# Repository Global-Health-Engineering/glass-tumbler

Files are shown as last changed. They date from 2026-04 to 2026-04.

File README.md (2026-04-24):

<!-- badges: start -->



<!-- badges: end -->

<h1> Solar-Powered Glass Tumbler for Cape Maclear, Malawi: Design, Maintenance, Operation, and Results </h1>

**Contributors**

- **Emma Steinke** &mdash; [ORCID 0009-0005-9115-9379](https://orcid.org/0009-0005-9115-9379) &mdash; *design, construction, testing, writing*
- **Jakub Tkaczuk** &mdash; [ORCID 0000-0001-7997-9423](https://orcid.org/0000-0001-7997-9423) &mdash; *supervision, page development & maintenance*
- **Elizabeth Tilley** &mdash; [ORCID 0000-0002-2095-9724](https://orcid.org/0000-0002-2095-9724) &mdash; *supervision*

<br>
<p align="middle">

<br><br>
This work is certified by the Open Source Hardware Association.<br \>

<br>
<b>Complete description of system design, functionalities, operation, and maintenance is available on:<br \>
<a href="https://global-health-engineering.github.io/glass-tumbler/">Github pages</a>.
</b>
</p>

# Background

This repository details the construction, operation, and maintenance of the solar-powered glass tumbler built as part of a collaboration between the Malawian community-based organization, Sustainable Cape Maclear, and the Global Health Engineering Group at ETH Zürich.

Cape Maclear is a rural Malawian town located within a UNESCO World Heritage Site, which has attracted significant tourism and growth in the last 20 years. This has led to a unique waste challenge: an abundance of non-returnable glass bottles that are not part of a deposit system. The accumulation of broken glass creates sharp fragments that pose significant injury risks to residents, tourists, and wildlife.

Because industrial recycling is not economically or technically feasible in this location, the tumbler uses **glass tumbling** to grind away sharp edges, producing smooth "sea glass" that is safe for reuse in construction, landscaping, and jewelry. The machine is a standalone, solar-powered rotating drum system designed to process 20 kg batches of glass with a total material cost of approximately **$581.10**.



# PDF Documentation

The full detailed guide and the quick start guide are available in the [`doc`](doc/) directory:

- [`doc/detailed_guide.pdf`](doc/detailed_guide.pdf)  
- [`doc/quickstart_guide.pdf`](doc/quickstart_guide.pdf)

CAD models and technical drawings are available in the [`cad`](cad/) directory.

# License

Different parts of this repository are released under different licenses, following standard practice for open-hardware research projects:

| Component | License |
| :--- | :--- |
| Hardware design (CAD, drawings, STEP files in [`cad/`](cad/)) | [CERN-OHL-S v2](LICENSE.md) |
| Documentation (qmd pages, guides in [`doc/`](doc/), this README) | [CC-BY-4.0](doc/LICENSE.md) |
| Datasets ([`data/`](data/)) | [CC-BY-4.0](data/LICENSE.md) |

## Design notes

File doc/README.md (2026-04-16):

# Documentation

PDF guides for the solar-powered glass tumbler.

| File | Description |
| :--- | :--- |
| [`detailed_guide.pdf`](detailed_guide.pdf) | Comprehensive manual covering the full system description, troubleshooting, electrical schematics, and repair procedures. |
| [`quickstart_guide.pdf`](quickstart_guide.pdf) | Short operator-facing guide for daily loading, running, and unloading of the tumbler. |

The rendered HTML version of the user-facing content lives on the project's [GitHub Pages site](https://global-health-engineering.github.io/glass-tumbler/).

## Licensing

The PDF guides in this directory are released under [Creative Commons Attribution 4.0 International (CC-BY-4.0)](LICENSE.md). The hardware design at the repository root is under [CERN-OHL-S v2](../LICENSE.md).

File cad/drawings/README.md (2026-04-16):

# Technical Drawings

2D manufacturing drawings for individual parts and the full assembly. All dimensions in millimetres.

| File | Contents |
| :--- | :--- |
| `fullTumbler.pdf` | Full assembly drawing with part callouts. |
| `mainFrame.pdf` | Outer (main) frame — 80 mm x 40 mm x 2 mm steel beams. |
| `innerFrame.pdf` | Inner (drum) frame — 30 mm x 30 mm x 2 mm steel beams. |
| `drumAndShaft.pdf` | Drum with shaft assembly (LPG cylinder body, 25 mm shaft). |
| `flange.pdf` | Custom lathe-turned flange connecting the shaft to the drum. |
| `drumLid.pdf` | Hexagonal drum lid with toggle-latch geometry and seal lining. |

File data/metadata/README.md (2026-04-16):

# GENERAL INFORMATION

* Title of Dataset: Solar-Powered Glass Tumbling Efficiency Analysis
* Author Information:
    * Name: Emma Steinke
    * Institution: Global Health Engineering Lab, ETH Zürich
    * Email: steinkee@ethz.ch

* Date of data collection: October 2025 - February 2026
* Geographic location of data collection: Cape Maclear, Malawi 

# SHARING/ACCESS INFORMATION

* Licenses/restrictions placed on the data: CC-BY
* Was data derived from another source? Yes
    * If yes, list source(s): Solar Irradiance data sourced from Solcast API.

# DATA & FILE OVERVIEW

## File List:
* **glass_brightness.csv**: Raw data containing pixel brightness measurements for glass samples at various tumbling durations.
* **imperfections.csv**: Raw counts of physical imperfections across different glass batches and abrasive media.
* **irradiance_data_2024.csv**: Meteorological data including Global Horizontal Irradiance (GHI), cloud opacity, and air temperature for the year 2024.
* **derived_lifetime_costs.csv**: Calculated financial projections comparing the cost per 100 kg of treated material over the system's lifetime.
* **glass_brightness_averages.csv**: Processed dataset providing the mean brightness values for each glass treatment category over time.
* **imperfections_averages.csv**: Processed dataset providing the average number of imperfections for each glass treatment category.
* **tumbler_start_260W.csv**: Start-up feasibility analysis for the tumbler using a single 260 W solar panel configuration.
* **tumbler_start_520W.csv**: Start-up feasibility analysis for the tumbler using a dual 520 W solar panel configuration.
* **tumbler_operational_stats.csv**: Yearly statistical distribution of daily operational runtimes for both the 260 W and 520 W power scenarios.

# METHODOLOGICAL INFORMATION
For a comprehensive breakdown of the experimental design, data collection protocols, and the theoretical framework supporting this study, please refer to the final master thesis report: **Development and Field Testing of a Solar-Powered Glass Tumbler for Waste Glass Processing in Cape Maclear, Malawi**.

## 1. Solar Panel Sizing and Operational Logic
The operational status for each hour ($S_{hr}$) was determined by comparing the available solar resource at Cape Maclear, Malawi, with the system's power demand. Local procurement in Blantyre identified 260 W panels as the standard available size. Consequently, the model evaluates the number of operational hours per day for both single (260 W) and dual (520 W) configurations using 2024 irradiance data.

**Operational Status Equation:**
$$S_{hr} = \begin{cases} 1 & \text{if } \left( \frac{G_{avail}}{1000} \right) \times P_{PV} \geq P_{peak} \\ 0 & \text{otherwise} \end{cases}$$

Where:
* **$G_{avail}$**: Hourly global horizontal irradiance ($W/m^2$).
* **$P_{PV}$**: Installed photovoltaic capacity (260 W or 520 W).
* **$P_{peak}$**: Required peak power for system operation (142.5 W).

A value of **1** indicates the solar resource is sufficient to meet the power demand, while **0** indicates a non-operational state.

## 2. Surface Clarity Analysis (Brightness/Fogginess)
Surface "fogginess" (the result of surface abrasion) was quantified through digital image processing. Post-tumbling, white glass samples were placed in a controlled-lighting environment in front of a black background and photographed.
* **Processing:** Square samples from the center of the glass piece were analyzed for mean pixel intensity.
* **Metric:** Values are expressed on a **Digital Number (DN)** scale from **0 to 255**. 
* **Interpretation:** Higher values (closer to 255) indicate a smoother, more reflective surface (polished), while lower values indicate a rougher, "foggier" surface caused by abrasive media.

## 3. Physical Integrity (Manual Imperfections)
To validate the efficacy of the abrasive media (Water, Sand, Silica Grit), a manual inspection protocol was established to count surface defects.
* **Sampling:** From each treatment batch, the **seven largest glass fragments** were selected for analysis.
* **Counting:** Each fragment was inspected for distinct physical imperfections such as conchoidal fractures. 
* **Averaging:** The final value represents the mean number of defects across those seven fragments per batch.

## 4. Total Cost of Ownership (Financial Analysis)
The financial viability of the system was modeled over its projected operational lifespan. The analysis accounts for both initial investment and recurring maintenance costs.
* **CAPEX (Capital Expenditure):** Costs associated with the solar panels, motor, structural frame, and tumbler drum.
* **OPEX (Operating Expenditure):** Maintenance requirements including scheduled applications of oil and grease for chain lubrication as well as labour costs. 
* **Normalization:** The final metric is calculated as the total lifetime cost divided by the total mass of glass processed, expressed in **USD per 100 kg**.

## Instrument- or software-specific information needed to interpret the data: 
Image Processing: Python 3.11.5
Analysis Environment: Python 3.11.5

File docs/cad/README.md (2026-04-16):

# CAD

CAD resources for the solar-powered glass tumbler.

## Subdirectories

- [`drawings/`](drawings/) — 2D technical drawings in PDF form, for manufacturing reference.
- [`step/`](step/) — 3D CAD assemblies exported in the neutral STEP (ISO 10303) format, openable in any major CAD package (SolidWorks, Fusion 360, FreeCAD, Onshape, etc.).

## Notes

- All dimensions are in millimetres unless annotated otherwise.
- The support wheel on the drum plate (added during field testing) and the outer-frame reinforcement beams are **not** present in these CAD files, as they were later modifications. See the construction guide for details.

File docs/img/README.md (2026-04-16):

# Images

Figures and logos used throughout the qmd pages, the README, and the rendered site.

## Photographs and figures

| File | Used in |
| :--- | :--- |
| `glassOnBeach.png` | index.qmd — broken glass on the beach. |
| `beforeAfter.png` | index.qmd — glass fragments before and after tumbling. |
| `tumblerOverview.png` | index.qmd, README — full tumbler overview render. |
| `fullTumblerAssembly.png` | construction.qmd — assembly drawing. |
| `frameAlignment.png` | construction.qmd — inner/outer frame alignment. |
| `reinforcement.png` | construction.qmd — outer-frame reinforcement beams. |
| `mainFrame.png` | construction.qmd — outer (main) frame drawing. |
| `gasCylinder.png` | construction.qmd — LPG cylinder cuts. |
| `shaftAttachment.png` | construction.qmd — flange dimensions and shaft attachment. |
| `extraWheel.png` | construction.qmd — additional support wheel. |
| `drumLid.png` | construction.qmd — hexagonal drum lid. |
| `motorHousing.png` | construction.qmd — drivetrain protected by housing. |
| `innerFrame.png` | construction.qmd — inner frame detail. |
| `electronicsOverview.png` | construction.qmd — electronics wiring layout. |
| `solarPanelStand.png` | construction.qmd — mobile adjustable solar panel stand. |
| `howtoTumble.png` | operation-maintenance.qmd — step-by-step tumbling procedure. |
| `howtoMaintain.png` | operation-maintenance.qmd — maintenance chart. |
| `glassTime.png` | results.qmd — visual progression of glass through tumbling time. |
| `artisans.png` | results.qmd — local artisan outcomes. |

## Logos and badges

| File | Purpose |
| :--- | :--- |
| `ETH_GHE_logo.svg` | Global Health Engineering Group / ETH Zürich logo, used in README. |
| `license-badge.svg` | CERN-OHL-S v2 license badge (generated with `badge-maker`). |

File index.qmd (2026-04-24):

---
title: "Solar-Powered Glass Tumbler for Cape Maclear, Malawi"
subtitle: "Design, Maintenance, Operation, and Results"
number-sections: true
format: html
---

<!-- badges: start -->
(https://ohwr.org/cern_ohl_s_v2.txt)
(https://creativecommons.org/licenses/by/4.0/)

<!-- badges: end -->

**Contributors**

- **Emma Steinke** &mdash; [ORCID 0009-0005-9115-9379](https://orcid.org/0009-0005-9115-9379) &mdash; *design, construction, testing, writing*
- **Jakub Tkaczuk** &mdash; [ORCID 0000-0001-7997-9423](https://orcid.org/0000-0001-7997-9423) &mdash; *supervision, page development & maintenance*
- **Elizabeth Tilley** &mdash; [ORCID 0000-0002-2095-9724](https://orcid.org/0000-0002-2095-9724) &mdash; *supervision*

<br>
<p align="middle">

<br><br> This work is certified by the Open Source Hardware
Association.\
(https://certification.oshwa.org/ch000030.html)
<br>
Github repository for this page sits [here](https://github.com/Global-Health-Engineering/glass-tumbler).
</p>

## Introduction

Cape Maclear is a rural Malawian town located within a UNESCO World Heritage Site, which has attracted a lot of tourism and growth in the last 20 years. This has led to a unique waste challenge: an abundance of non-returnable glass bottles that are not part of a deposit system. As shown in Figure 1, this broken glass creates sharp fragments that pose significant injury risks to residents, tourists, and wildlife.

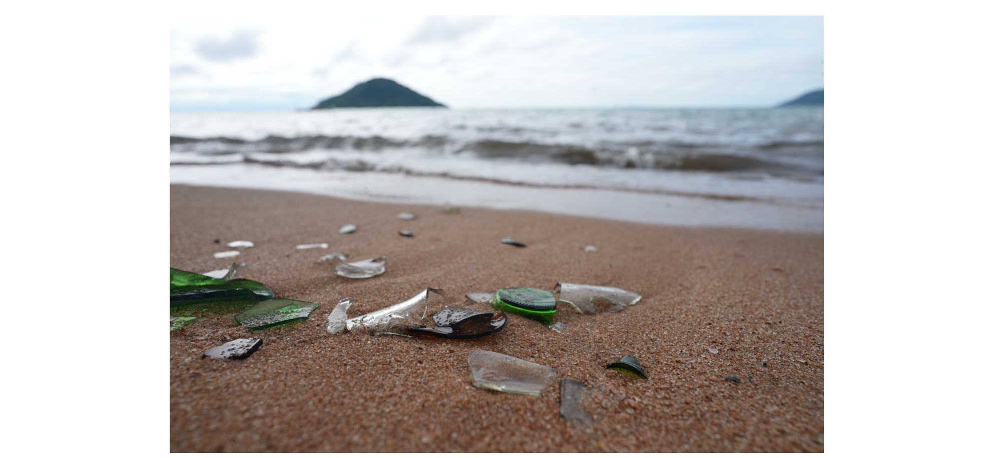
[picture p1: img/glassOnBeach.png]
Figure 1: Accumulation of broken glass on the beach


Because industrial recycling is not economically or technically feasible in this location, this project utilizes **glass tumbling** to grind away sharp edges. This process produces smooth "sea glass," which is safe for reuse in construction, landscaping, and jewelry. The transformation from sharp fragments to smooth glass is illustrated in Figure 2.

Figure 2: Glass fragments before and after the tumbling process

## Tumbler Overview

The machine is a standalone, solar-powered rotating drum system designed to process batches of glass. An overview of the full assembly can be seen in Figure 3.

Figure 3: Overview of the glass tumbler assembly

The system operates through five core stages:

1. **Solar Harvesting**: A 260 W solar panel generates DC electricity from sunlight.
2. **Power Regulation**: An electronics box containing a DC-DC converter and PWM motor controller stabilizes the variable solar voltage to a consistent 24 V.
3. **Mechanical Drive**: A 350 W 24 V DC motor converts electrical energy into rotational motion.
4. **Power Transmission**: A bicycle chain and sprocket system transmits torque to a shaft attached to the rear of the drum.
5. **Rotating Drum**: A 19 kg LPG cylinder serves as the tumbling vessel.

### Key Specifications

* **Capacity**: The drum has a volume of 38.5 l and can processes **20 kg** of glass per batch (typically requiring 8–10 hours of tumbling for the best finish). It operates with the drum being around half-full.  
* **Operating Speed**: The drum is typically run at 40 RPM but can reach speeds up to 57 RPM. 
* **Direct Solar (Battery-Free) Design**: The system operates without a battery buffer, making the motor's performance directly dependent on real-time solar irradiance. When sunlight is abundant, the tumbler maintains its preset operating speed. If irradiance drops—due to cloud cover, panel shading, or a suboptimal angle of inclination—the system slows down accordingly. 

## Part List

The total cost to manufacture the system is approximately **$581.10**. A detailed breakdown of the components, specifications, and procurement origins is provided in the table below.

| Item | Specification | Origin | Qty | Unit (\$) | Total (\$) |
| :--- | :--- | :---: | :---: | :---: | :---: |
| **Drivetrain** | | | | | **56.50** |
| DC Motor | 350 W | CH | 1 | 48.00 | 48.00 |
| Sprocket | Bicycle 410, 48T | MW | 1 | 5.30 | 5.30 |
| Chain | 1/2" x 1/8" x 114 L | MW | 1 | 3.20 | 3.20 |
| **Electronics** | | | | | **123.00** |
| DC-DC Converter | 50 A, 1000 W | CH | 1 | 41.00 | 41.00 |
| PWM Controller | 10 – 55 V | CH | 1 | 22.00 | 22.00 |
| Circuit Breakers | 25 A | CH | 3 | 9.00 | 27.00 |
| Ring Ferrules | 3, 4, 5 mm ID | CH | 20 | 0.13 | 2.50 |
| Fuses | 10 A | CH | 2 | 0.25 | 0.50 |
| Tachometer | Model BC 120 | CH | 1 | 20.00 | 20.00 |
| Volt/Amp Meter | 0–100 V, 50 A | CH | 2 | 5.00 | 10.00 |
| **Finishing** | | | | | **85.10** |
| Enclosure | 350 mm x 250 mm x 200 mm | MW | 1 | 6.70 | 6.70 |
| Motor Cover | 460 mm x 350 mm x 250 mm | MW | 1 | 6.60 | 6.60 |
| Lid Seal | 10 mm x 12 mm | CH | 1 | 16.00 | 16.00 |
| Surface Treat. | 2K Paint/Red Oxide | MW | 1 | 55.80 | 55.80 |
| **Housing** | | | | | **222.80** |
| Gas Cylinder | 19 kg (300 mm ID) | MW | 1 | 78.90 | 78.90 |
| Steel Beam (L) | 80 mm x 40 mm x 2 mm (6 m) | MW | 1 | 44.50 | 44.50 |
| Steel Beam (S) | 30 mm x 30 mm x 2 mm (6 m) | MW | 1 | 23.70 | 23.70 |
| Steel Sheet | 460 mm x 200 mm x 5 mm | MW | 1 | 9.20 | 9.20 |
| Bearings | 25 mm ID | CH | 1 | 0.00 | 0.00 |
| Shaft | 25 mm OD | CH | 1 | 0.00 | 0.00 |
| Steel Offcuts | Various Dimensions | MW | 1 | 8.90 | 8.90 |
| Castor Wheels | Ø 100 mm | MW | 2 | 2.10 | 4.20 |
| Small Wheel | 50 mm x 19 mm | CH | 1 | 4.00 | 4.00 |
| Toggle Clamp | 150 kg Capacity | CH | 4 | 5.00 | 20.00 |
| Lid Metal | 400 mm x 400 mm x 3 mm | MW | 1 | 7.90 | 7.90 |
| Fasteners | M6, M8, M10 | MW | 1 | 10.30 | 10.30 |
| Welding Rods | Ø 2.5 mm | MW | 1 | 11.20 | 11.20 |
| **Solar PV** | | | | | **93.70** |
| Solar Panel | 260 W | MW | 1 | 69.70 | 69.70 |
| Connectors | MC4 Standard | CH | 6 | 4.00 | 24.00 |
| **GRAND TOTAL** | | | | | **$581.10** |

**COO Key:** MW = Malawi (Local Procurement), CH = Switzerland (Imported)

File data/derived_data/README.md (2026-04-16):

# Derived Data

Datasets produced from [`../raw_data/`](../raw_data/) by analysis scripts. These feed the figures and tables in [`results.qmd`](../../results.qmd).

| File | Description | Derived from |
| :--- | :--- | :--- |
| `glass_brightness_averages.csv` | Mean pixel brightness per (abrasive medium × tumbling time) group. | `glass_brightness.csv` |
| `imperfections_averages.csv` | Mean imperfection count across the seven largest fragments per batch. | `imperfections.csv` |
| `tumbler_start_260W.csv` | Hourly binary indicator (0/1) of whether a single 260 W panel provides sufficient irradiance to start the motor, for each hour of 2024. | `irradiance_data_2024.csv` |
| `tumbler_start_520W.csv` | Same as above for a dual-panel 520 W configuration. | `irradiance_data_2024.csv` |
| `tumbler_operational_stats.csv` | Distribution of daily operational hours over the year, for the 260 W and 520 W scenarios. | `tumbler_start_260W.csv`, `tumbler_start_520W.csv` |
| `derived_lifetime_costs.csv` | Lifetime cost per 100 kg of tumbled glass under different assumed system lifetimes and panel configurations. | Cost model (see `../metadata/README.md`, §4). |

Variable definitions, units, and value ranges are documented in [`../metadata/codebook.csv`](../metadata/codebook.csv). Methodology is documented in [`../metadata/README.md`](../metadata/README.md).

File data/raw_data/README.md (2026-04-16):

# Raw Data

Unprocessed measurements from field trials and external sources. These files are the authoritative inputs to everything in [`../derived_data/`](../derived_data/).

| File | Description | Source |
| :--- | :--- | :--- |
| `glass_brightness.csv` | Pixel-brightness measurements of individual tumbled glass samples across durations and abrasive media. | Digital image processing of photographs taken under controlled lighting. |
| `imperfections.csv` | Manual counts of surface imperfections on the seven largest glass fragments per batch. | Visual inspection of post-tumbling fragments. |
| `irradiance_data_2024.csv` | Hourly Global Horizontal Irradiance (GHI), cloud opacity, and air temperature for Cape Maclear, Malawi, throughout 2024. | [Solcast API](https://solcast.com/). |

Variable definitions, units, and value ranges are documented in [`../metadata/codebook.csv`](../metadata/codebook.csv).

## Conventions

- Timestamps in `irradiance_data_2024.csv` are UTC (ISO 8601), matching the Solcast export.
- Tumbling durations (`time_h`, `Hours`) are whole hours from batch start.
- Do not modify files in this directory — analyses should read from here and write to `../derived_data/`.

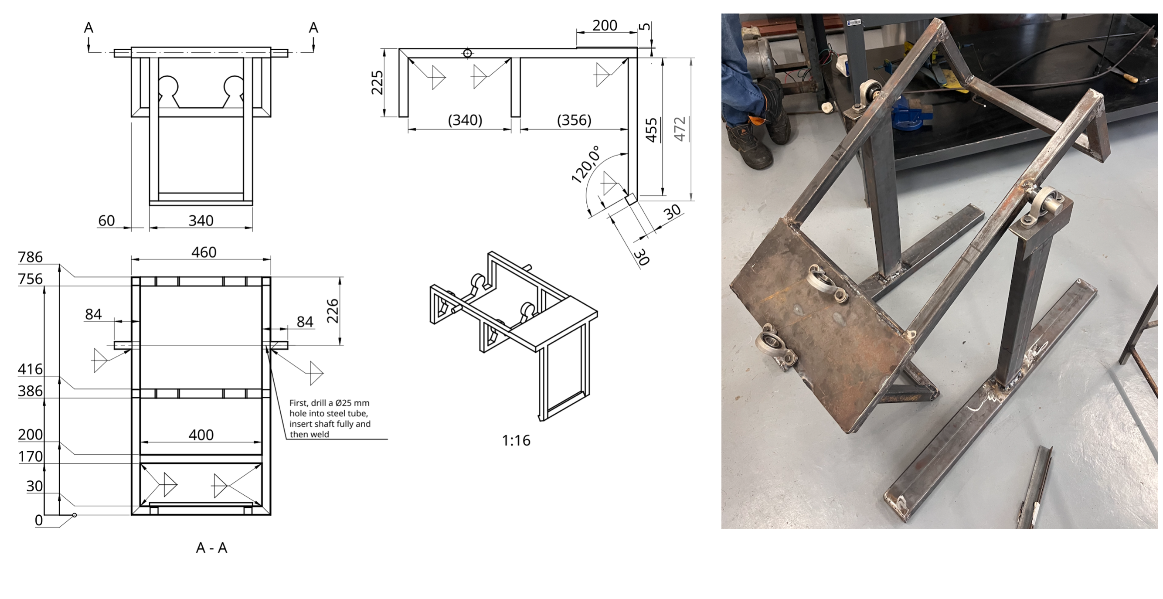
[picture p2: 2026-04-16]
docs/img/innerFrame.png

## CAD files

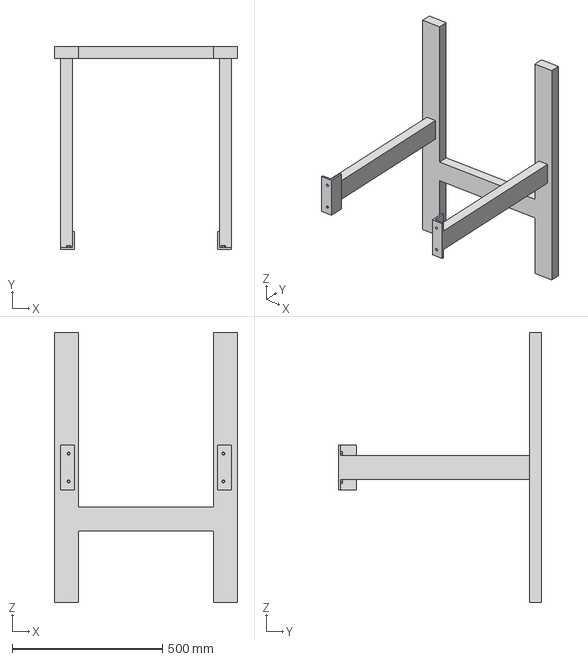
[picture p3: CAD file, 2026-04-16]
docs/cad/step/Main Frame.step
610.0 x 677.0 x 900.0 mm

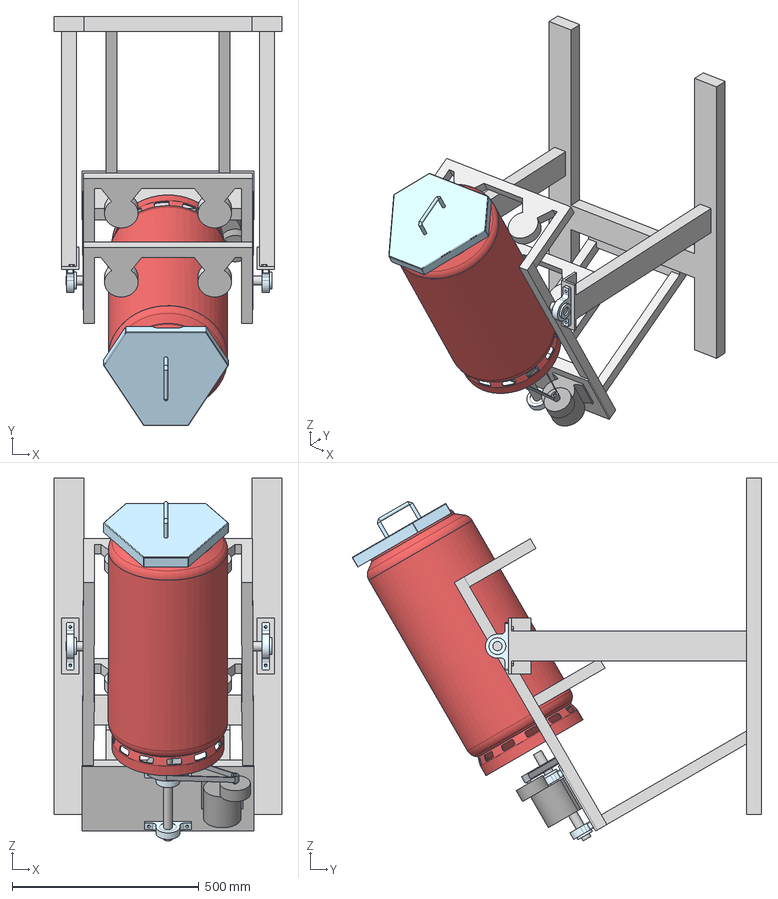
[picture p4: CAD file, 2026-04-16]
docs/cad/step/Tumbler Assembly.step
610.0 x 1095.1 x 971.6 mm
Motor
Bearing 1 x 3
Drum x 2
Motor Pulley
Barrel Lid
Drum Frame
Frame
Shaft
Bearing 2
Belt bottom
Belt top
Drum Pulley

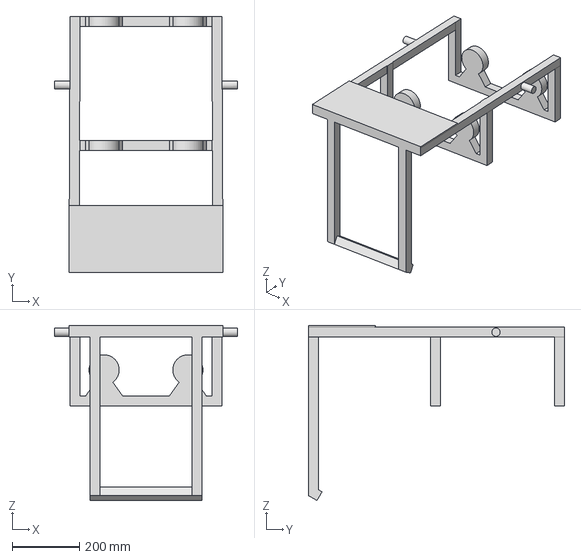
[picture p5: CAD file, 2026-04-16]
docs/cad/step/Drum Frame.step
546.0 x 765.0 x 522.3 mm

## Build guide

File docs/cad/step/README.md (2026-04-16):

# STEP Files

3D CAD assemblies in the neutral STEP (ISO 10303) format. These can be opened in any modern CAD package (SolidWorks, Fusion 360, FreeCAD, Onshape, etc.).

| File | Contents |
| :--- | :--- |
| `Tumbler Assembly.step` | Full tumbler assembly (outer frame + inner frame + drum + drivetrain mount). |
| `Main Frame.step` | Outer (main) frame sub-assembly. |
| `Drum Frame.step` | Inner (drum) frame sub-assembly with bearing backplate. |

## Not represented in the CAD model

- The auxiliary support wheel added to the drum plate after field testing.
- The outer-frame reinforcement and crossbeams added after initial welding.
- The lockable motor/drivetrain housing built in Malawi.

See `construction.qmd` (or the detailed guide PDF) for these additions.

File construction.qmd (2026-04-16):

---
title: "Construction Guide"
number-sections: true
format: html
---

**Note:** The CAD model of the assembly and the PDF versions of all drawings are available in the [`cad`](https://github.com/Global-Health-Engineering/glass-tumbler/tree/main/cad) directory of the GitHub repository.

The mechanical design of the tumbler is inspired by a concrete mixer configuration to enable ease of loading and unloading glass. The following two tutorials on building DIY concrete mixers served as primary sources of inspiration:

* [Design using an 11 kg gas cylinder as a drum](https://www.youtube.com/watch?v=cXIDimhZ2z8)
* [Design using an oil barrel as a drum](https://youtu.be/vJwhrh9DE5g?si=aXEkfoyNJi_KFIie)

If you intend to build a similar design, watching these videos is highly recommended, as they provide valuable insights into the manufacturing process.

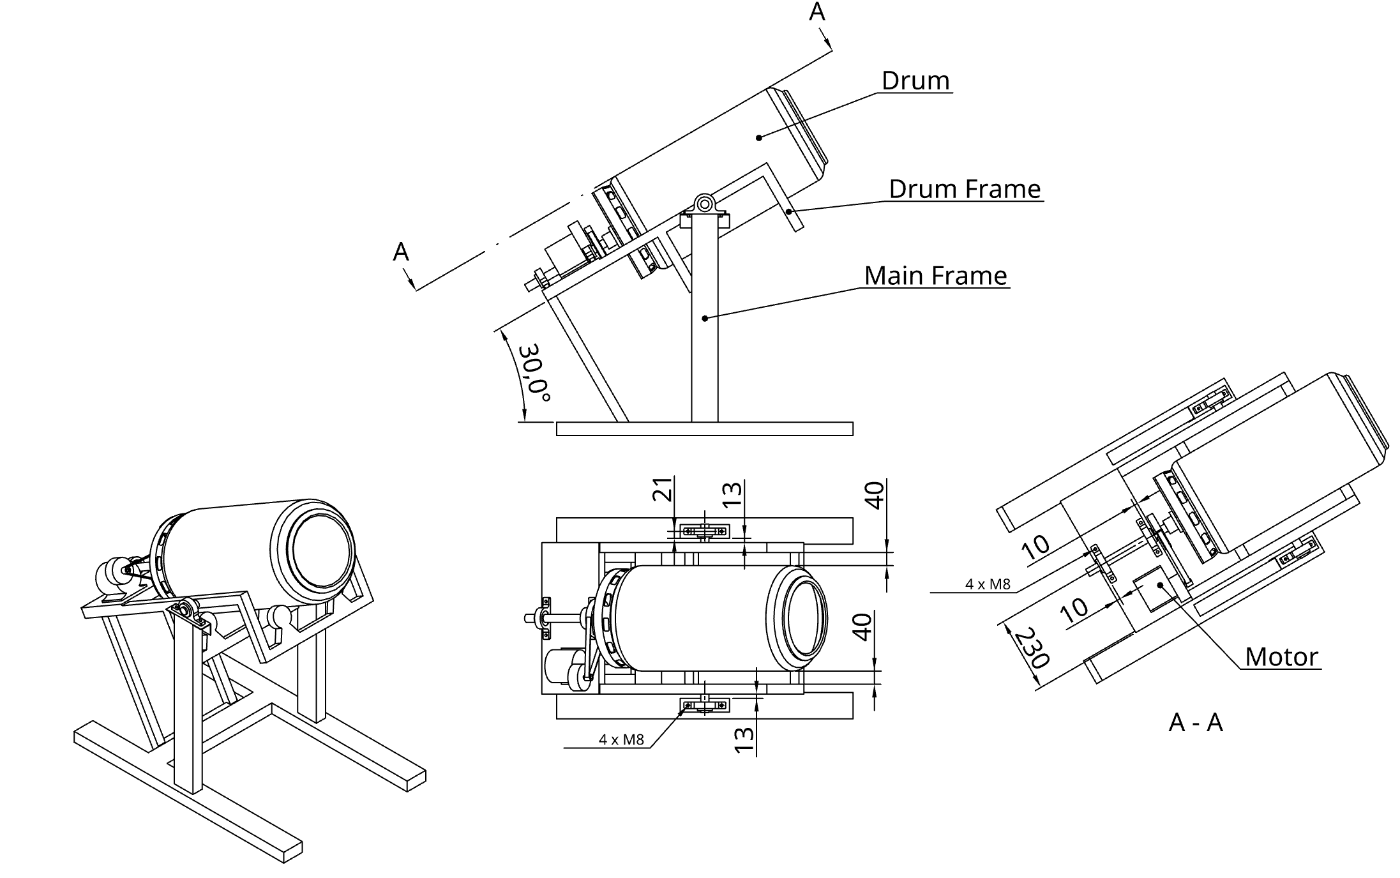
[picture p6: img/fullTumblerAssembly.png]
Figure 1: Full Tumbler Assembly


Figure 1 shows the final assembly drawing of the tumbler with its individual components. The wall thickness of all metal components is at least 2 mm to facilitate easier welding.

## Frames

First, the inner (drum) frame is constructed from 30 mm x 30 mm x 2 mm (height x width x thickness) steel beams. The dimensions are shown in Figure 2. Although the technical drawing includes two sets of castor wheels, one set is actually sufficient; the rear section holding the second set may be omitted. A metal plate is mounted at the back of the inner frame to hold the bearings and the motor. In this specific build, a 5 mm thick plate was used. To ensure a stronger weld for the 25 mm shafts, two 25 mm holes were pre-drilled for the shafts to sit in. Because the ideal position of the castor wheels depends on their specific size, their attachment points should be adjustable. It is best to attach these during a later phase once the drum shaft is seated on the inner frame.

Next, the legs of the outer frame are constructed from 80 mm x 40 mm x 2 mm steel beams. To increase weld strength, two 80 mm x 40 mm slots are cut into the base beams so the legs can be inserted into the feet before welding.

The two main bearings are attached to the outer frame legs using angle irons and M8 bolts. Two additional bearings are attached to the front and back of the inner frame’s backplate to support the drum shaft. The inner frame is then aligned between the two legs to determine the final length of the connection beams. **Note:** The two legs of the outer frame should only be welded together while the inner frame is positioned between them (see Figure 2).

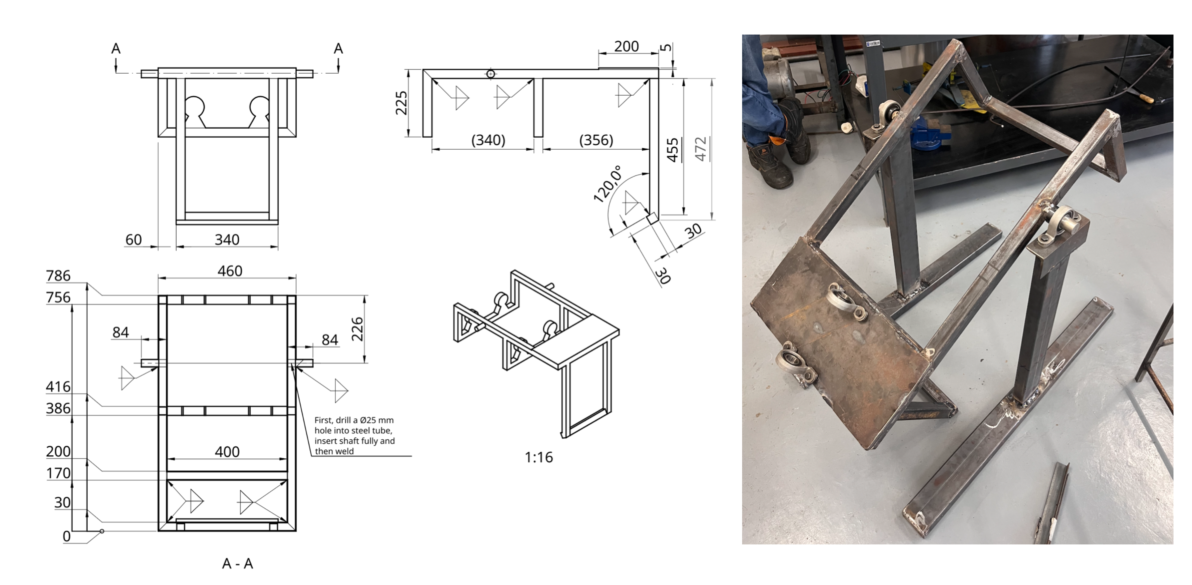
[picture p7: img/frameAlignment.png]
Figure 2: Technical drawing of the inner frame and alignment with the legs of the outer frame


Once the first connection beam is welded, additional reinforcement beams can be added (see Figure 3). In this design, the outer frame is further reinforced with beams at the base and crossbeams to stabilize the legs. This step is highly recommended if sufficient material is available.

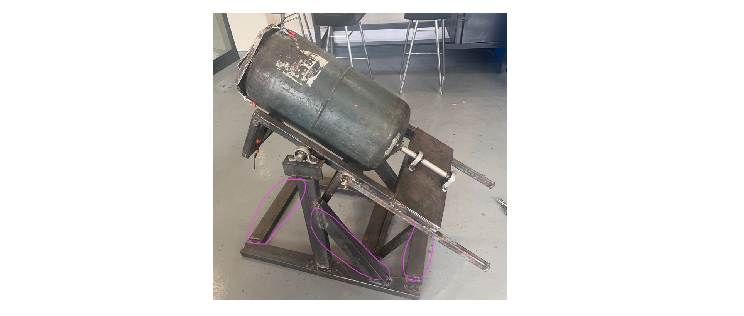
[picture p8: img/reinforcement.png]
Figure 3: Further reinforcement beams in the outer frame


Figure 4 provides the dimensions and additional manufacturing notes for the outer (main) frame. Note that it does not contain the reinforcement beams as these were added after the CAD design had been completed. 

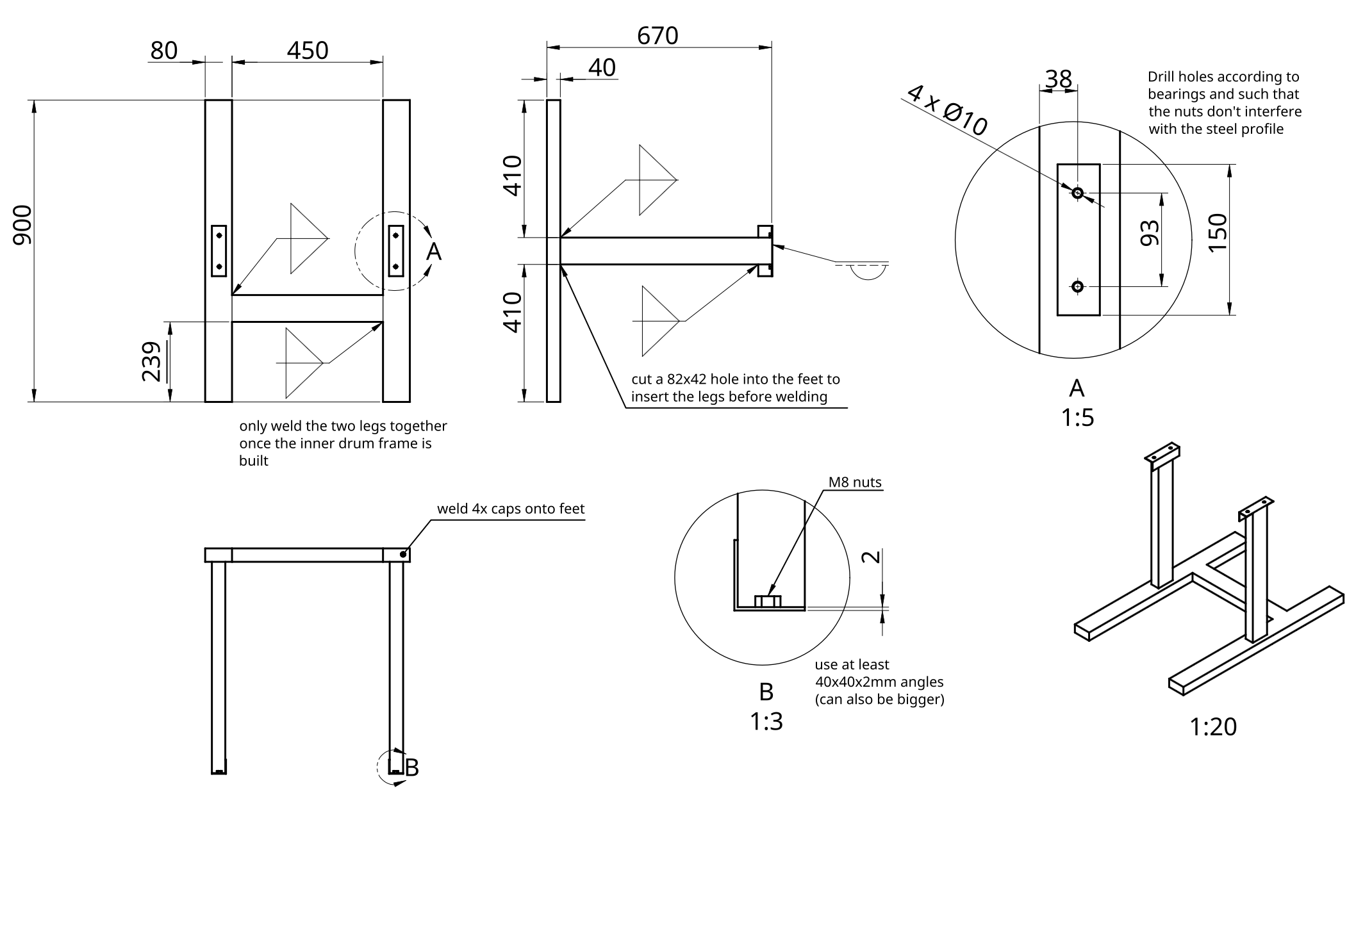
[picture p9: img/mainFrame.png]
Figure 4: Technical drawing of outer (main) frame


## Drum

A 19 kg LPG cylinder (32 cm diameter, 85 cm height) was chosen for its wall thickness and abrasion resistance. As this is an uncommon size, it was sourced via Facebook Marketplace in Blantyre.

**Safety Warning:** Ensure all gas has been completely purged from the cylinder. This is achieved by opening the valve and letting it vent overnight (after all usable gas is exhausted). The cylinder must then be filled completely with water and emptied to displace any remaining gas pockets. This step is critical for safety before cutting.

Once the drum is completely purged, use an angle grinder to make several cuts (see Figure 5):

1. Cut the top lip off from the top of the cylinder; this will be reused as the rim for the new opening.
2. Remove the handle.
3. Cut a round hole the size of the handle.
4. Remove the base.

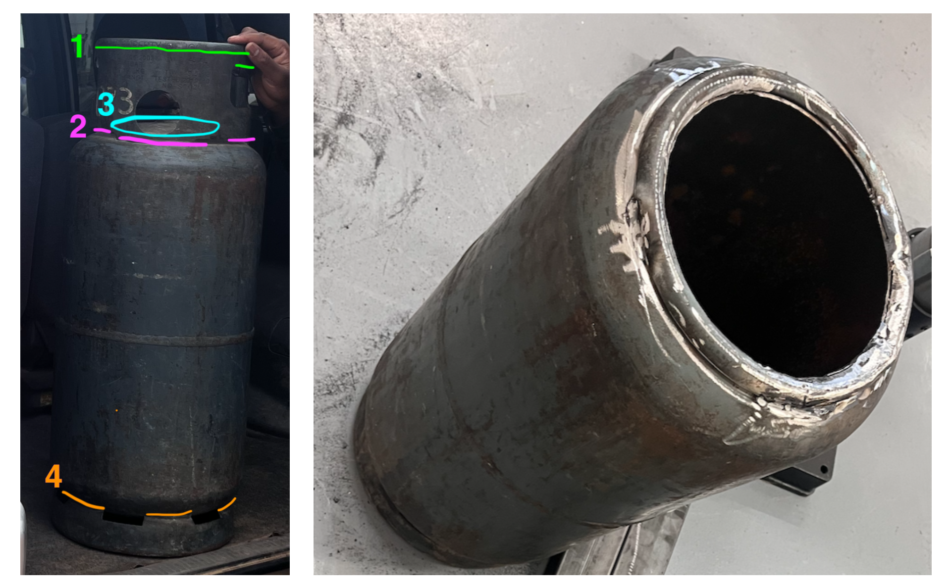
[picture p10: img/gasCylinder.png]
Figure 5: Gas cylinder cuts and lip welded on to the top


Once these cuts are complete, the lip removed from the top can be welded back onto the newly cut hole (see Figure 5).

The next step is to attach the shaft to the back of the drum. This must be done with great precision to ensure the shaft's axis is perfectly aligned with the drum's axis. A custom flange was fabricated using a lathe (see Figure 6) and welded onto the 25 mm shaft. While initial attempts were made to weld the flange directly to the drum, this resulted in warping and axial misalignment. Consequently, four holes were drilled into the drum, and the flange was secured using four M6 bolts. These holes were sealed with epoxy putty on both the interior and exterior to ensure the drum remains watertight. Final tightening and alignment should be performed while the drum is mounted to the inner frame. By rotating the drum manually, you can check for wobbling; minor misalignments can be corrected by placing thin metal shims under the bolts.

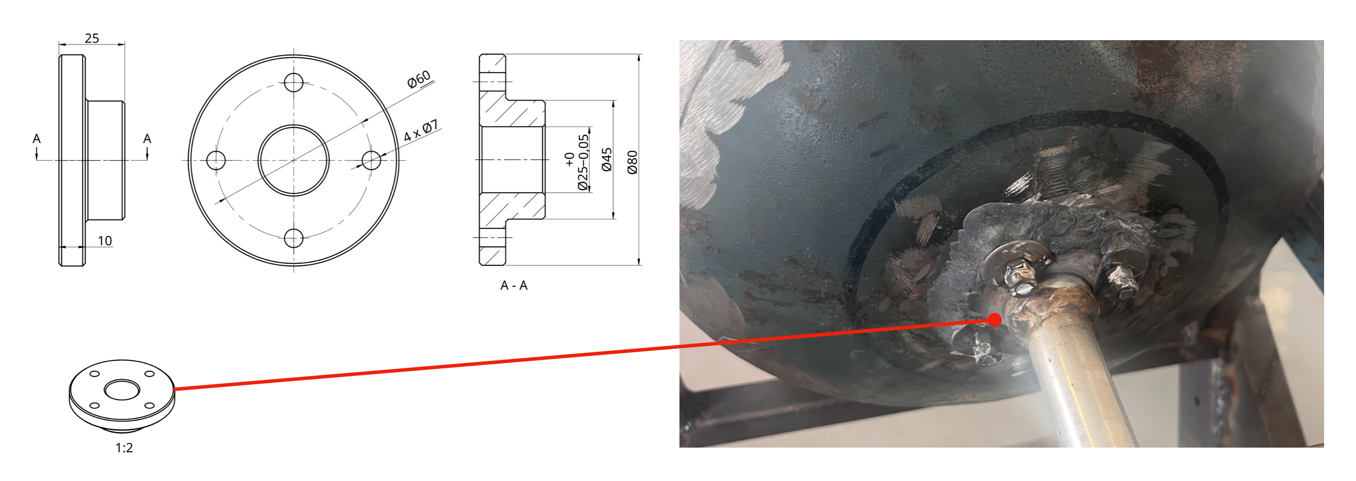
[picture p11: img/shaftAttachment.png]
Figure 6: Dimensions of the custom flange and final shaft attachment


Although the bearing seats are designed to prevent axial displacement, a heavy load of glass puts immense pressure on these seats, which may loosen over time and cause the drum to slide backward. To prevent this, an additional support wheel (see Figure 7) was added to the inner frame's drum plate. As this was a later modification, it is not shown in the CAD model.

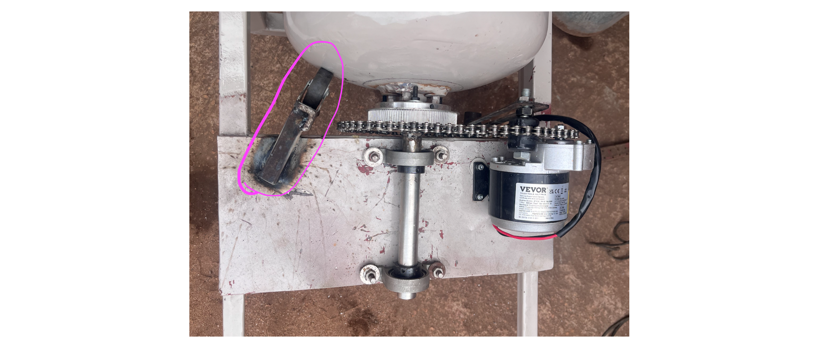
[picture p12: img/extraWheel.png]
Figure 7: Extra wheel


### Drum Lid

The lid features a hexagonal design where the inner triangle fits snugly around the drum's lip, and the outer triangle aligns with the toggle latches on the drum wall (see Figure 8). The interior is lined with a rubber seal (standard door/window weatherstripping).

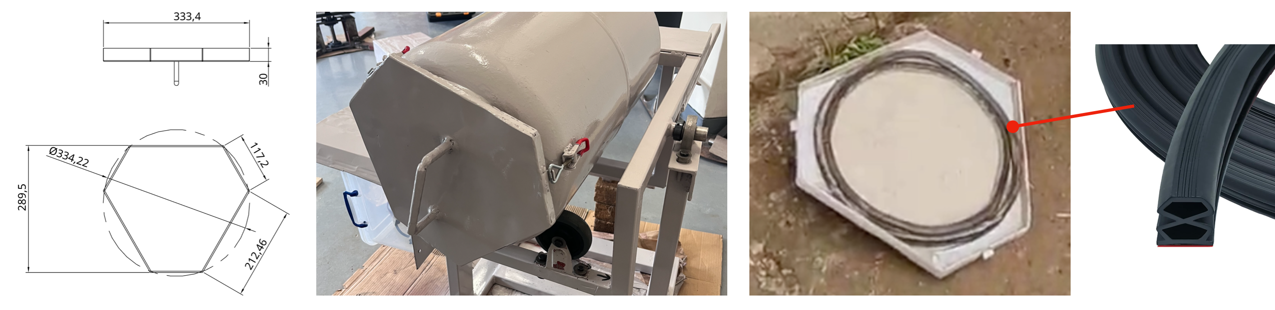
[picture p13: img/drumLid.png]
Figure 8: Dimensions of lid, as attached to the drum with toggle latches, lid lining


## Drivetrain

Although a belt drive was initially planned, it proved unreliable, and the system was converted to a **bicycle chain drive**. The gear ratio from the motor to the bike sprocket is 1:6. While the sprocket can be welded directly to the shaft, this often causes warping, resulting in poor chain rotation. Instead, the sprocket is bolted to a connection part that is itself welded to the shaft. A chain tensioner was also added to allow for adjustments (see Figure 9). Once the drivetrain was completed, a lockable protective cover was added to prevent theft and protect the motor. This housing includes a door for easy access during maintenance and repairs.

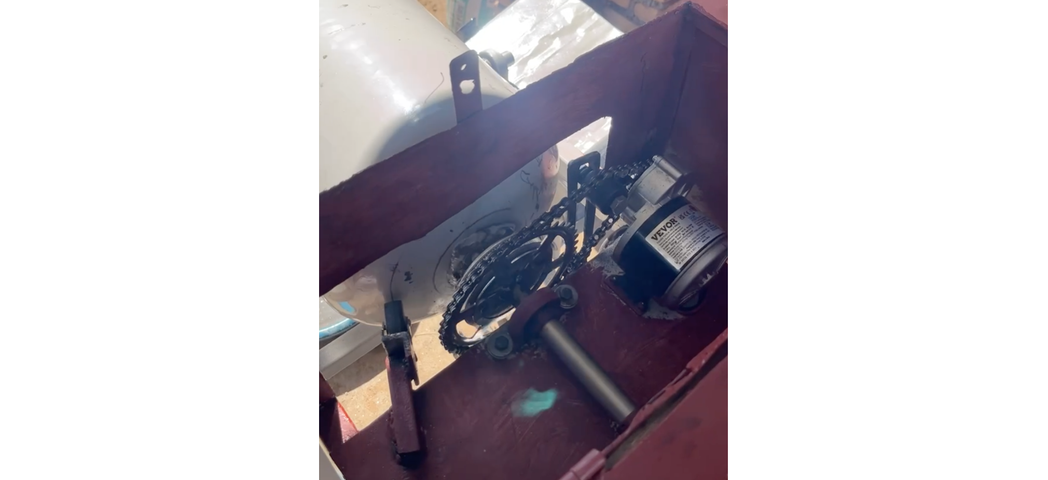
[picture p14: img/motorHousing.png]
Figure 9: Drivetrain as built protected by the housing


## Electronics

The following electronic components were used:

* **[24 V DC Motor](https://amzn.eu/d/06L4CkVM):** A 350 W motor with an integrated planetary gearbox (310 RPM max). With the 1:6 gear ratio, the speed is reduced to approximately 51 RPM, which is ideal for a 30 cm diameter drum (the optimal range is 35–50 RPM). Testing showed the tumbler uses a maximum of 110 W when full, so a less powerful motor would also suffice.
* **[DC-DC Converter](https://amzn.eu/d/0bTFwdRn):** A high-capacity 1000 W converter with an integrated cooling fan. When selecting a converter, ensure the solar panel voltage fits within the input range (25–90 V in this case) and the motor's nominal voltage fits the output range (2.5–50 V). An oversized converter is recommended to prevent overheating during long operation cycles. The output voltage is tuned via a potentiometer screw on the unit.
* **[PWM Controller](https://amzn.eu/d/0d9MLGuE):** This model features an integrated on/off switch, LED display, and speed control knob. Ensure the controller is compatible with your motor's voltage and rated current.
* **Solar Panel:** The system is powered by a 260 W solar panel featuring a maximum power voltage ($V_{mp}$) of 41.3 V and an open-circuit voltage ($V_{oc}$) of 49.2 V. While a second identical panel was purchased and can be wired in parallel to double the available solar capacity, a single-panel configuration proved sufficient for most weather conditions during testing.
* **[50 A Circuit Breaker](https://amzn.eu/d/0d3LKDwU), [25 A Circuit Breaker](https://amzn.eu/d/0czYagVh)**: DC-rated circuit breakers were used to protect and easily isolate the circuit.
* **[Voltmeter/Ammeter](https://amzn.eu/d/03LGwiDu):** Used to monitor voltage and current before and after the converter. While optional, it is very helpful for troubleshooting and monitoring power consumption.
* **[Bicycle Tachometer](https://www.decathlon.ch/de/p/velocomputer-kabellos-bc-120/346167/m8799862):** Used to keep track of the total rotations the tumbler performed (as this is weather-dependant). It is also an optional component that was simply helpful for data collection purposes.

The electronics were wired according to the layout shown in Figure 10, which also illustrates the component placement within the electronics box. For all primary power connections, standard **10 AWG (6 mm²)** solar wire was used, terminated with corresponding ring ferrules to ensure secure and low-resistance contact points.

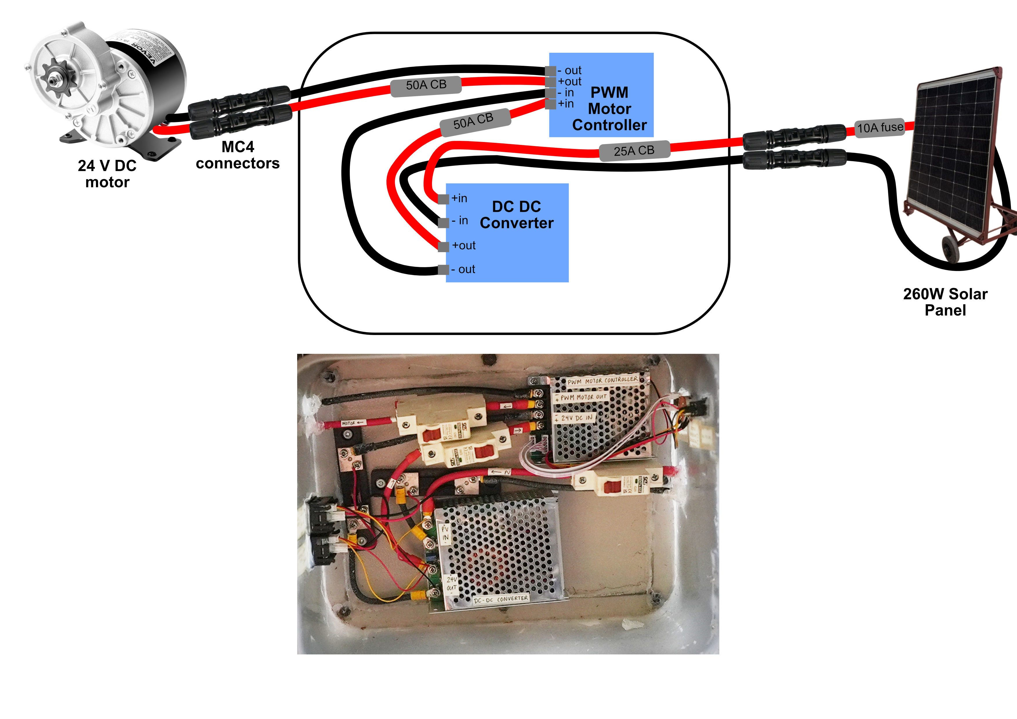
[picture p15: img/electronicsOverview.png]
Figure 10: Electronics


For a more comprehensive explanation, please refer to the [**Detailed Guide PDF**](doc/detailed_guide.pdf), specifically Section 4: Detailed System Description, located in the [`doc`](https://github.com/Global-Health-Engineering/glass-tumbler/tree/main/doc) directory of the GitHub repository.

## Solar Panel Stand

Because the operating site in Cape Maclear is not monitored overnight, the solar panel is stored indoors when not in use. To facilitate this, a mobile and adjustable solar panel stand was constructed, as shown in Figure 11. It was constructed using 40 mm angle irons. 

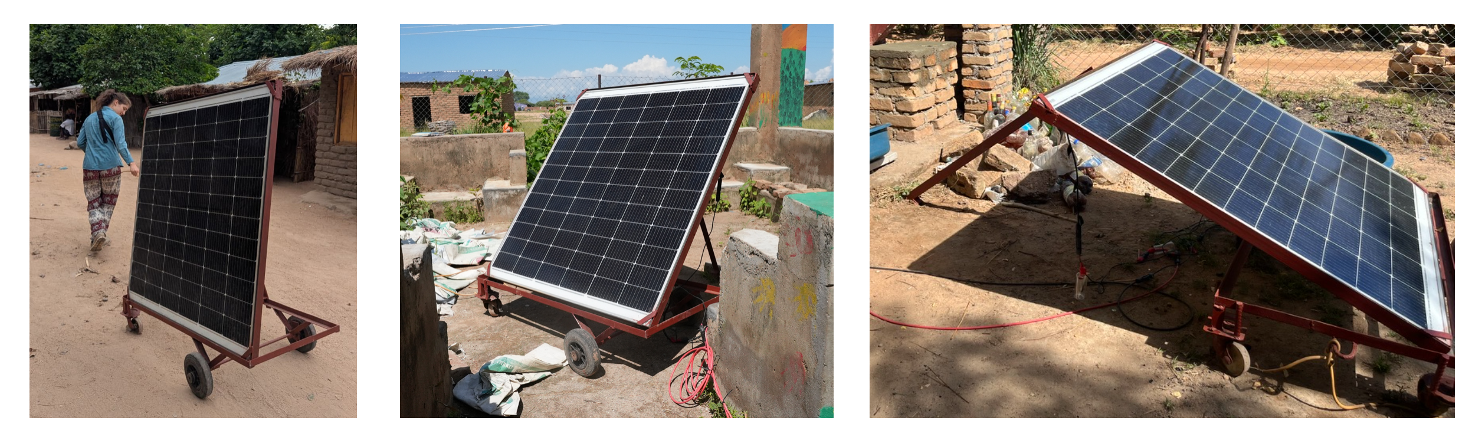
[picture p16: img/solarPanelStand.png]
Figure 11: Solar panel stand at different angles of inclination


The stand is equipped with four wheels — two fixed wheelbarrow wheels for stability on uneven terrain and two rotating castor wheels — allowing the entire assembly to be easily transported between the storage location and the tumbler. Additionally, the stand features a hinged frame and a support leg that allow the solar panel to be tilted to the optimal angle for maximum solar intake throughout the day.

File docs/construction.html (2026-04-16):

# Construction Guide

Note: The CAD model of the assembly and the PDF versions of all drawings are available in the cad (https://github.com/Global-Health-Engineering/glass-tumbler/tree/main/cad) directory of the GitHub repository.

The mechanical design of the tumbler is inspired by a concrete mixer configuration to enable ease of loading and unloading glass. The following two tutorials on building DIY concrete mixers served as primary sources of inspiration:

- Design using an 11 kg gas cylinder as a drum (https://www.youtube.com/watch?v=cXIDimhZ2z8)
- Design using an oil barrel as a drum (https://youtu.be/vJwhrh9DE5g?si=aXEkfoyNJi_KFIie)

If you intend to build a similar design, watching these videos is highly recommended, as they provide valuable insights into the manufacturing process.



Figure 1: Full Tumbler Assembly

Figure 1 shows the final assembly drawing of the tumbler with its individual components. The wall thickness of all metal components is at least 2 mm to facilitate easier welding.

## 1 Frames

First, the inner (drum) frame is constructed from 30 mm x 30 mm x 2 mm (height x width x thickness) steel beams. The dimensions are shown in Figure 2. Although the technical drawing includes two sets of castor wheels, one set is actually sufficient; the rear section holding the second set may be omitted. A metal plate is mounted at the back of the inner frame to hold the bearings and the motor. In this specific build, a 5 mm thick plate was used. To ensure a stronger weld for the 25 mm shafts, two 25 mm holes were pre-drilled for the shafts to sit in. Because the ideal position of the castor wheels depends on their specific size, their attachment points should be adjustable. It is best to attach these during a later phase once the drum shaft is seated on the inner frame.

Next, the legs of the outer frame are constructed from 80 mm x 40 mm x 2 mm steel beams. To increase weld strength, two 80 mm x 40 mm slots are cut into the base beams so the legs can be inserted into the feet before welding.

The two main bearings are attached to the outer frame legs using angle irons and M8 bolts. Two additional bearings are attached to the front and back of the inner frame’s backplate to support the drum shaft. The inner frame is then aligned between the two legs to determine the final length of the connection beams. Note: The two legs of the outer frame should only be welded together while the inner frame is positioned between them (see Figure 2).



Figure 2: Technical drawing of the inner frame and alignment with the legs of the outer frame

Once the first connection beam is welded, additional reinforcement beams can be added (see Figure 3). In this design, the outer frame is further reinforced with beams at the base and crossbeams to stabilize the legs. This step is highly recommended if sufficient material is available.



Figure 3: Further reinforcement beams in the outer frame

Figure 4 provides the dimensions and additional manufacturing notes for the outer (main) frame. Note that it does not contain the reinforcement beams as these were added after the CAD design had been completed.



Figure 4: Technical drawing of outer (main) frame

## 2 Drum

A 19 kg LPG cylinder (32 cm diameter, 85 cm height) was chosen for its wall thickness and abrasion resistance. As this is an uncommon size, it was sourced via Facebook Marketplace in Blantyre.

Safety Warning: Ensure all gas has been completely purged from the cylinder. This is achieved by opening the valve and letting it vent overnight (after all usable gas is exhausted). The cylinder must then be filled completely with water and emptied to displace any remaining gas pockets. This step is critical for safety before cutting.

Once the drum is completely purged, use an angle grinder to make several cuts (see Figure 5):

1. Cut the top lip off from the top of the cylinder; this will be reused as the rim for the new opening.
2. Remove the handle.
3. Cut a round hole the size of the handle.
4. Remove the base.



Figure 5: Gas cylinder cuts and lip welded on to the top

Once these cuts are complete, the lip removed from the top can be welded back onto the newly cut hole (see Figure 5).

The next step is to attach the shaft to the back of the drum. This must be done with great precision to ensure the shaft’s axis is perfectly aligned with the drum’s axis. A custom flange was fabricated using a lathe (see Figure 6) and welded onto the 25 mm shaft. While initial attempts were made to weld the flange directly to the drum, this resulted in warping and axial misalignment. Consequently, four holes were drilled into the drum, and the flange was secured using four M6 bolts. These holes were sealed with epoxy putty on both the interior and exterior to ensure the drum remains watertight. Final tightening and alignment should be performed while the drum is mounted to the inner frame. By rotating the drum manually, you can check for wobbling; minor misalignments can be corrected by placing thin metal shims under the bolts.



Figure 6: Dimensions of the custom flange and final shaft attachment

Although the bearing seats are designed to prevent axial displacement, a heavy load of glass puts immense pressure on these seats, which may loosen over time and cause the drum to slide backward. To prevent this, an additional support wheel (see Figure 7) was added to the inner frame’s drum plate. As this was a later modification, it is not shown in the CAD model.



Figure 7: Extra wheel

### 2.1 Drum Lid

The lid features a hexagonal design where the inner triangle fits snugly around the drum’s lip, and the outer triangle aligns with the toggle latches on the drum wall (see Figure 8). The interior is lined with a rubber seal (standard door/window weatherstripping).



Figure 8: Dimensions of lid, as attached to the drum with toggle latches, lid lining

## 3 Drivetrain

Although a belt drive was initially planned, it proved unreliable, and the system was converted to a bicycle chain drive. The gear ratio from the motor to the bike sprocket is 1:6. While the sprocket can be welded directly to the shaft, this often causes warping, resulting in poor chain rotation. Instead, the sprocket is bolted to a connection part that is itself welded to the shaft. A chain tensioner was also added to allow for adjustments (see Figure 9). Once the drivetrain was completed, a lockable protective cover was added to prevent theft and protect the motor. This housing includes a door for easy access during maintenance and repairs.



Figure 9: Drivetrain as built protected by the housing

## 4 Electronics

The following electronic components were used:

- 24 V DC Motor (https://amzn.eu/d/06L4CkVM): A 350 W motor with an integrated planetary gearbox (310 RPM max). With the 1:6 gear ratio, the speed is reduced to approximately 51 RPM, which is ideal for a 30 cm diameter drum (the optimal range is 35–50 RPM). Testing showed the tumbler uses a maximum of 110 W when full, so a less powerful motor would also suffice.
- DC-DC Converter (https://amzn.eu/d/0bTFwdRn): A high-capacity 1000 W converter with an integrated cooling fan. When selecting a converter, ensure the solar panel voltage fits within the input range (25–90 V in this case) and the motor’s nominal voltage fits the output range (2.5–50 V). An oversized converter is recommended to prevent overheating during long operation cycles. The output voltage is tuned via a potentiometer screw on the unit.
- PWM Controller (https://amzn.eu/d/0d9MLGuE): This model features an integrated on/off switch, LED display, and speed control knob. Ensure the controller is compatible with your motor’s voltage and rated current.
- Solar Panel: The system is powered by a 260 W solar panel featuring a maximum power voltage (\(V_{mp}\)) of 41.3 V and an open-circuit voltage (\(V_{oc}\)) of 49.2 V. While a second identical panel was purchased and can be wired in parallel to double the available solar capacity, a single-panel configuration proved sufficient for most weather conditions during testing.
- 50 A Circuit Breaker (https://amzn.eu/d/0d3LKDwU), 25 A Circuit Breaker (https://amzn.eu/d/0czYagVh): DC-rated circuit breakers were used to protect and easily isolate the circuit.
- Voltmeter/Ammeter (https://amzn.eu/d/03LGwiDu): Used to monitor voltage and current before and after the converter. While optional, it is very helpful for troubleshooting and monitoring power consumption.
- Bicycle Tachometer (https://www.decathlon.ch/de/p/velocomputer-kabellos-bc-120/346167/m8799862): Used to keep track of the total rotations the tumbler performed (as this is weather-dependant). It is also an optional component that was simply helpful for data collection purposes.

The electronics were wired according to the layout shown in Figure 10, which also illustrates the component placement within the electronics box. For all primary power connections, standard 10 AWG (6 mm²) solar wire was used, terminated with corresponding ring ferrules to ensure secure and low-resistance contact points.



Figure 10: Electronics

For a more comprehensive explanation, please refer to the Detailed Guide PDF, specifically Section 4: Detailed System Description, located in the doc (https://github.com/Global-Health-Engineering/glass-tumbler/tree/main/doc) directory of the GitHub repository.

## 5 Solar Panel Stand

Because the operating site in Cape Maclear is not monitored overnight, the solar panel is stored indoors when not in use. To facilitate this, a mobile and adjustable solar panel stand was constructed, as shown in Figure 11. It was constructed using 40 mm angle irons.



Figure 11: Solar panel stand at different angles of inclination

The stand is equipped with four wheels — two fixed wheelbarrow wheels for stability on uneven terrain and two rotating castor wheels — allowing the entire assembly to be easily transported between the storage location and the tumbler. Additionally, the stand features a hinged frame and a support leg that allow the solar panel to be tilted to the optimal angle for maximum solar intake throughout the day.

This project was supported by the Global Health Engineering Group at ETH Zurich (https://ghe.ethz.ch)

- (https://github.com/Global-Health-Engineering/glass-tumbler)
- (https://matrix.to/#/#ghe-open:staffchat.ethz.ch)

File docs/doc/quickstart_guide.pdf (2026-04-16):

# Glass Tumbler Quick Start Guide

## Parts you should have

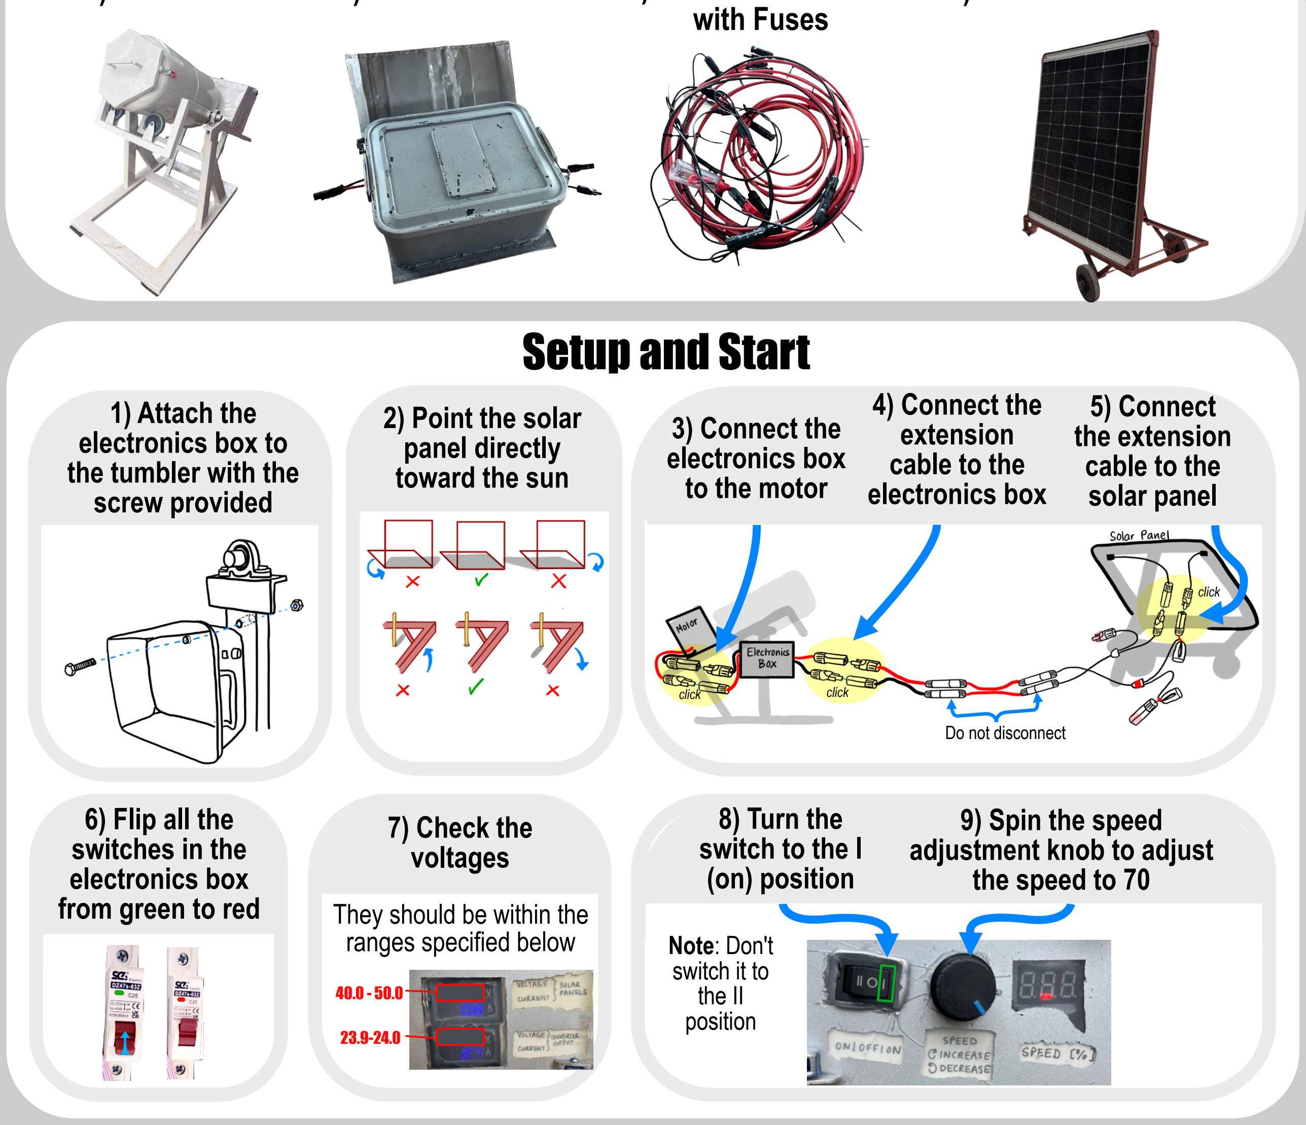
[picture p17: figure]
1) Attach the electronics box to the tumbler with the screw provided; Setup and Start; 2) Point the solar panel directly toward the sun; They should be within the ranges specified below; click; with Fuses; 3) Connect the electronics box to the motor; 4) Connect the extension cable to the electronics box; 5) Connect the extension cable to the solar panel; 6) Flip all the switches in the electronics box from green to red; 7) Check the voltages; 8) Turn the switch to the I (on) position; 9) Spin the speed adjustment knob to adjust the speed to 70; Note: Don't switch it to the II position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

When You Leave | Important Rules
3) Connection Cables
2) Electronics Box
4) Solar Panel on Stand
1) Glass Tumbler
1. Turn off the tumbler by reducing the speed to 0 and flipping the switch to the off (o) position
2. Flip all switches in the electronics from red to green
3. Disconnect the cables in the three places where you connected them
4. Lock the motor box
5. Store the solar panel and electronics box in a safe place
6. Empty out all glass and water from the tumbler (otherwise you will create rust)

Never connect the solar panel cables directly to the motor. The electronics box must always be in between.

Stop operation if you hear loud or unusual noises

No hands near the moving chain

Keep water away from the electronics box

Never leave the electronics box or the solar panel unattended

Always disconnect the motor from the electronics box when emptying the tumbler (the cable is not long enough)

# Malangizo Ofulumira Oyambitsa Tumbler ya Galasi

## Zida zofunika

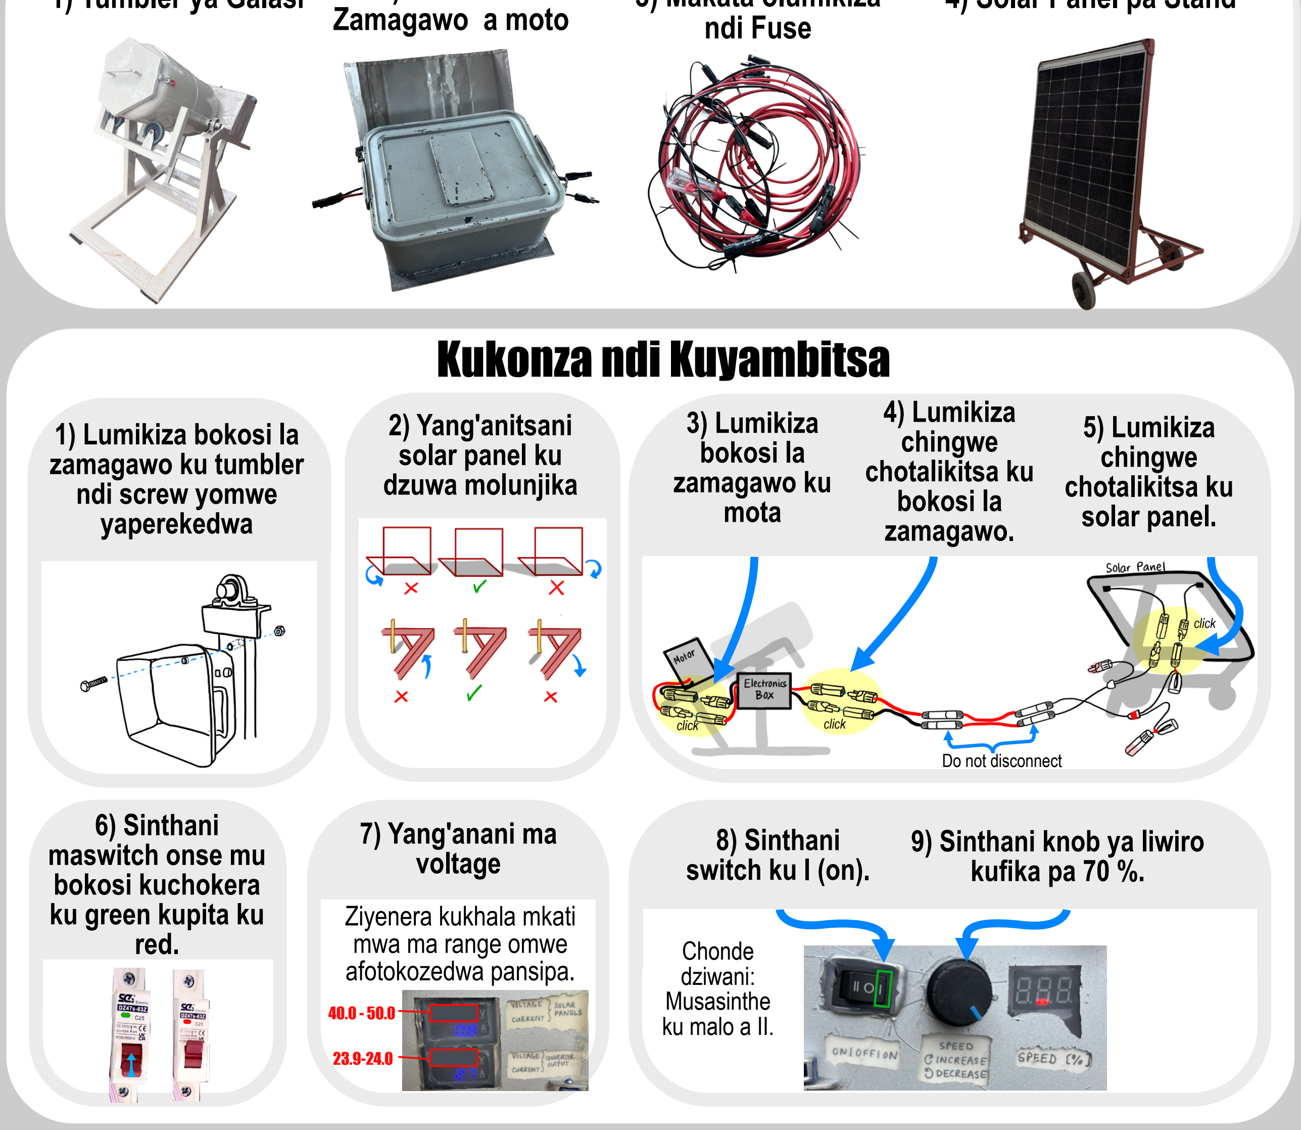
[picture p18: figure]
1) Lumikiza bokosi la zamagawo ku tumbler ndi screw yomwe yaperekedwa; Kukonza ndi Kuyambitsa; 2) Yang'anitsani solar panel ku dzuwa molunjika; Ziyenera kukhala mkati mwa ma range omwe afotokozedwa pansipa.; click; Do not disconnect; ndi Fuse; Zamagawo a moto; 3) Lumikiza bokosi la zamagawo ku mota; 4) Lumikiza chingwe chotalikitsa ku bokosi la zamagawo.; 5) Lumikiza chingwe chotalikitsa ku solar panel.; 6) Sinthani maswitch onse mu bokosi kuchokera ku green kupita ku red.; 7) Yang'anani ma voltage; 8) Sinthani switch ku I (on).; 9) Sinthani knob ya liwiro kufika pa 70 %.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
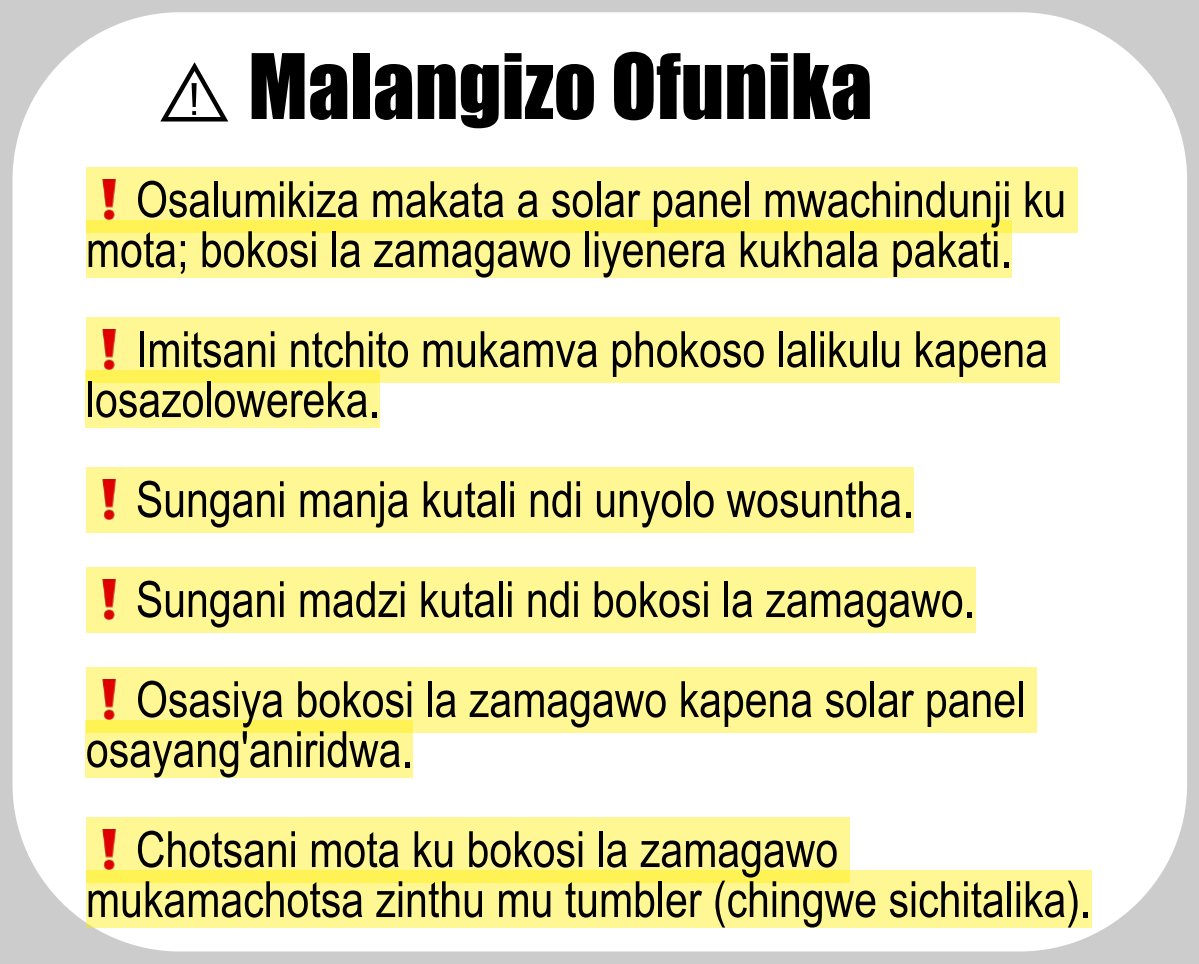
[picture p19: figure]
losazolowereka.; osayang'aniridwa.; Chotsani mota ku bokosi la zamagawo

Zoyenera kuchita mukasiya | Malangizo Ofunika
3) Makata olumikiza
2) Bokosi la
4) Solar Panel pa Stand
1) Tumbler ya Galasi
1. Chepetsani liwiro kufika pa 0 ndi kusuntha switch ku off (0).
2. Sinthani maswitch onse kuchokera ku red kupita ku green.
3. Chotsani makata pamalo atatu olumikizira.
4. Tsekani bokosi la mota.
5. Sungani solar panel ndi bokosi la zamagawo pamalo otetezeka.
6. Chotsani galasi ndi madzi mu tumbler kuti mupewe dzimbiri.

Osalumikiza makata a solar panel mwachindunji ku mota; bokosi la zamagawo liyenera kukhala pakati.

Imitsani ntchito mukamva phokoso lalikulu kapena

Sungani manja kutali ndi unyolo wosuntha.

Sungani madzi kutali ndi bokosi la zamagawo.

Osasiya bokosi la zamagawo kapena solar panel

mukamachotsa zinthu mu tumbler (chingwe sichitalika).

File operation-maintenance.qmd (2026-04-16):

---
title: "Operation and Maintenance Guide"
number-sections: true
format: html
---

This guide provides a visual overview of how to operate and maintain the solar-powered glass tumbler. 

## How to Tumble Glass

The following graphic explains the step-by-step process for loading, processing, and unloading glass to achieve a smooth "sea glass" finish.

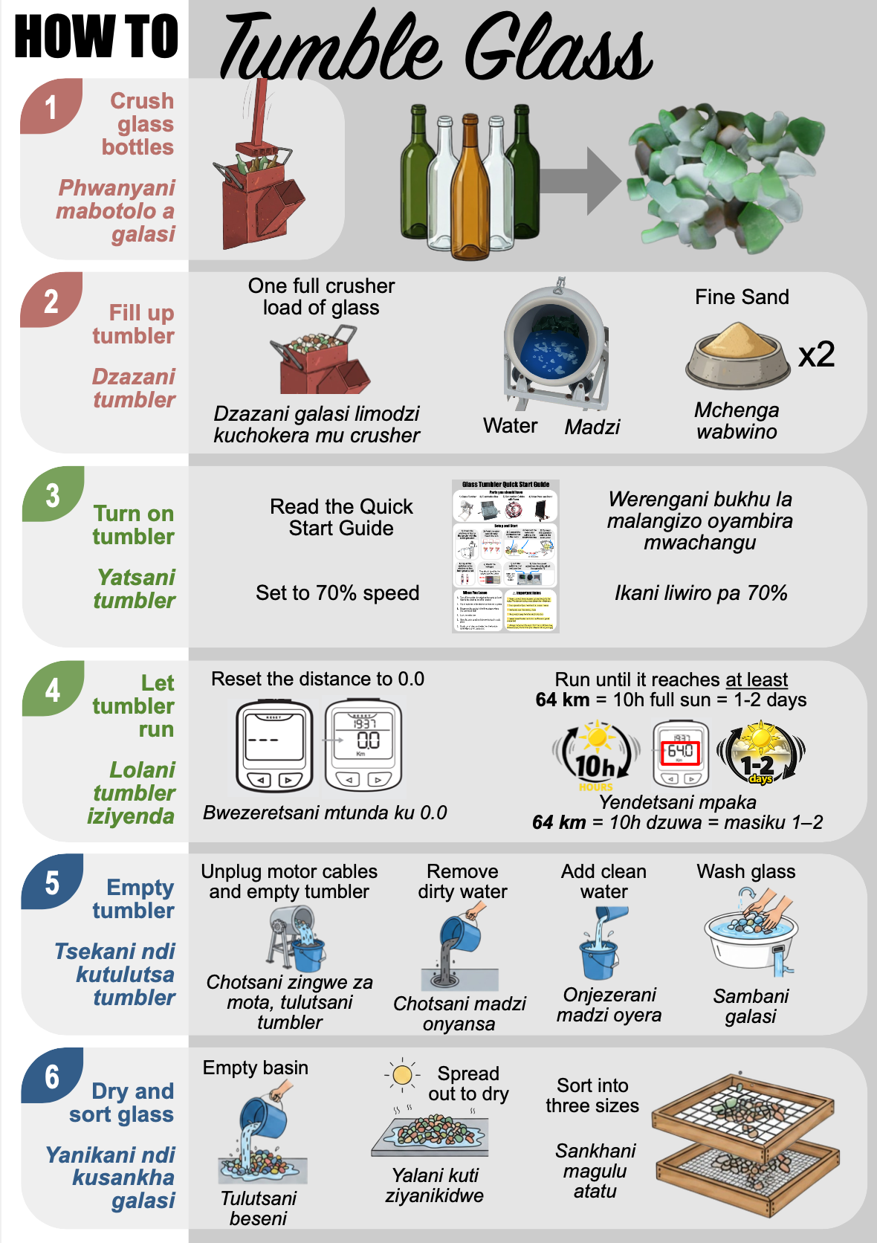
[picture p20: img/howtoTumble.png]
Figure 1: How to Tumble Glass


The [quick start guide](doc/quickstart_guide.pdf) for this tumbler design can be found on the GitHub repository in the [`doc`](https://github.com/Global-Health-Engineering/glass-tumbler/tree/main/doc) directory.

## How to Maintain the Tumbler

Regular maintenance ensures the longevity of the machine and the safety of the operator. Please refer to the maintenance chart below for maintenance tasks.

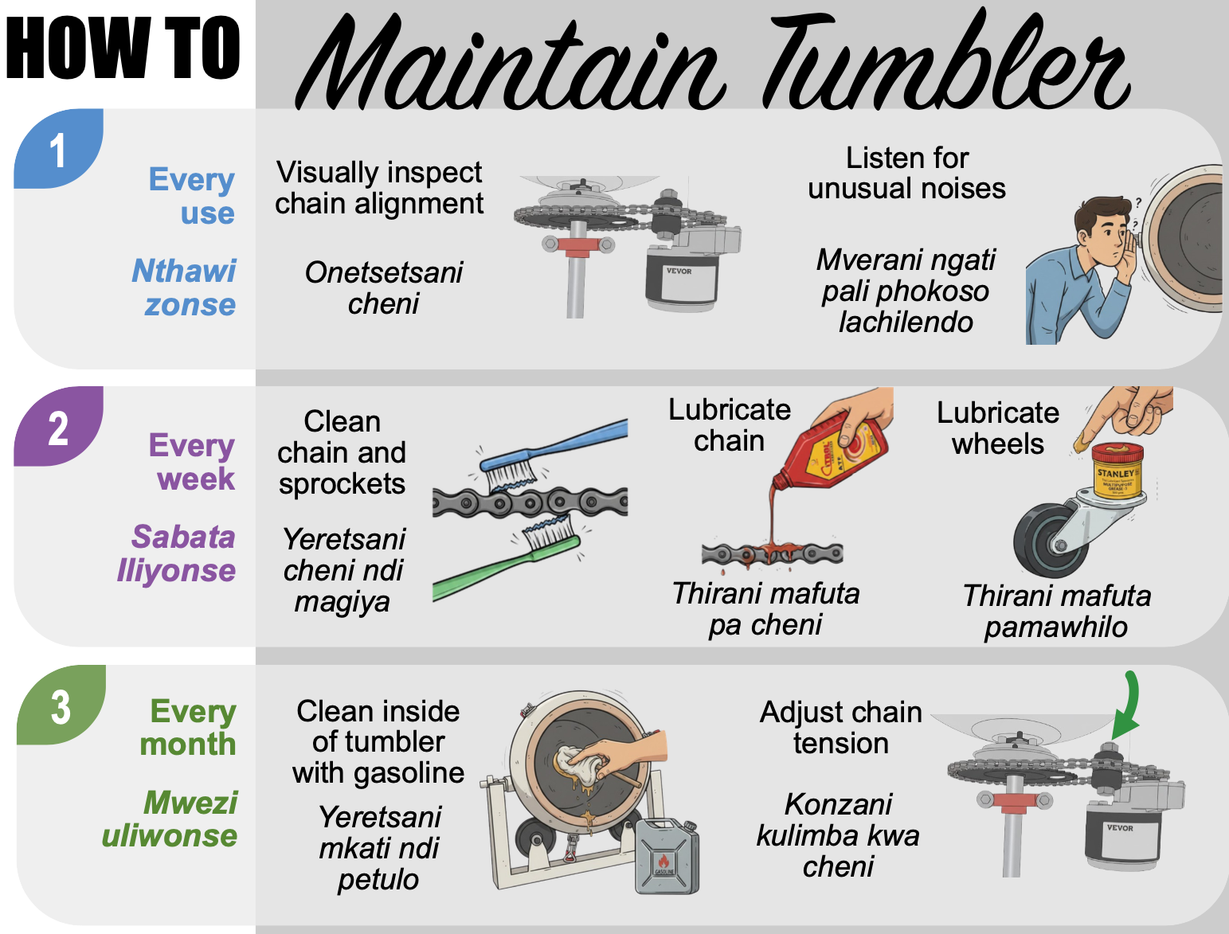
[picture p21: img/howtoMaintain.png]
Figure 2: Maintenance Guide


## Troubleshooting

In the event of a mechanical failure, electrical issue, or unexpected behavior of the machine, do not attempt unauthorized repairs. All diagnostic procedures, electrical schematics, and repair instructions are located in the comprehensive troubleshooting manual in this GitHub repository: [**Detailed Guide PDF**](doc/detailed_guide.pdf).
*See **Section 2: Troubleshooting** for specific guidance on resolving system issues.*

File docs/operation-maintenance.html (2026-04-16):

# Operation and Maintenance Guide

This guide provides a visual overview of how to operate and maintain the solar-powered glass tumbler.

## 1 How to Tumble Glass

The following graphic explains the step-by-step process for loading, processing, and unloading glass to achieve a smooth “sea glass” finish.



Figure 1: How to Tumble Glass

The quick start guide for this tumbler design can be found on the GitHub repository in the doc (https://github.com/Global-Health-Engineering/glass-tumbler/tree/main/doc) directory.

## 2 How to Maintain the Tumbler

Regular maintenance ensures the longevity of the machine and the safety of the operator. Please refer to the maintenance chart below for maintenance tasks.



Figure 2: Maintenance Guide

## 3 Troubleshooting

In the event of a mechanical failure, electrical issue, or unexpected behavior of the machine, do not attempt unauthorized repairs. All diagnostic procedures, electrical schematics, and repair instructions are located in the comprehensive troubleshooting manual in this GitHub repository: Detailed Guide PDF. See Section 2: Troubleshooting for specific guidance on resolving system issues.

This project was supported by the Global Health Engineering Group at ETH Zurich (https://ghe.ethz.ch)

- (https://github.com/Global-Health-Engineering/glass-tumbler)
- (https://matrix.to/#/#ghe-open:staffchat.ethz.ch)

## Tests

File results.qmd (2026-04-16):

---
title: "Results"
number-sections: true
format: html
---

This page summarizes the performance, operational lessons and financial viability of the solar-powered glass tumbler based on data collected in February 2026.

## Operational Performance

During its initial deployment from February 3 to February 27, the tumbler was operational for **118.5 hours**. It successfully produced nine batches of tumbled glass, with each batch weighing approximately 20 kg. The process effectively transforms sharp, hazardous glass shards into smooth, safe "sea glass".

## Process Optimization

Experimental trials were conducted to determine the most efficient parameters for a high-quality finish:

* **Optimal Duration**: A 10-hour cycle is recommended to maximize quality. While much of the smoothing happens in the first few hours, "tumbledness" reaches a point of diminishing returns at the 8 to 10-hour mark (see Figure 1).
* **Abrasive Media**: The addition of a fine abrasive is mandatory for a nice finish. Trials using "just water" resulted in increased structural damage to the glass.
* **Viability of Local Sand**: Locally sourced fine sand performed nearly as well as industrial silicon grit. Given its zero cost and high availability in Malawi, local sand is the superior choice.

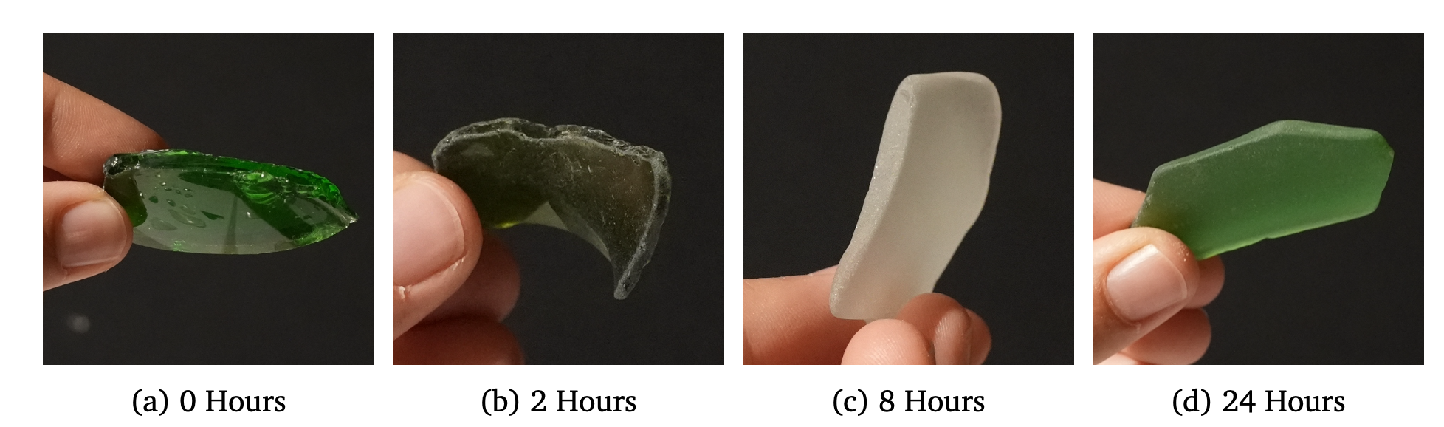
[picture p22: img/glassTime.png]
Figure 1: Glass progression


## System Efficiency

* **Power Draw**: At the standard operating speed of 40 RPM, the system maintains a constant power draw of **79 W**. Even at 100% speed, the draw was 107.1 W.
* **Annual Yield**: A single-panel (260 W) setup is projected to yield **4'274 kg per year**, while a dual-panel (520 W) setup can reach **5'060 kg per year**.

## Financial Viability

The total material cost (CAPEX) for the standard 260 W system was **$581.10**. The **Minimum Viable Price** represents the break-even point required to cover all annual operating costs and amortized construction costs over a 5-year equipment lifetime.

| Metric | 260 W Setup | 520 W Setup |
| :--- | :---: | :---: |
| Annual Yield | 4'274 kg  | 5'060 kg  |
| **Minimum Viable Price (USD per 100 kg)** | **$4.94** | **$4.40**  |

## Reuse and Creative Outcomes

Tumbled glass is already being integrated into the local economy in Cape Maclear. Local artisans have explored the material's creative potential, producing jewelry and decorative items (see Figure 2).

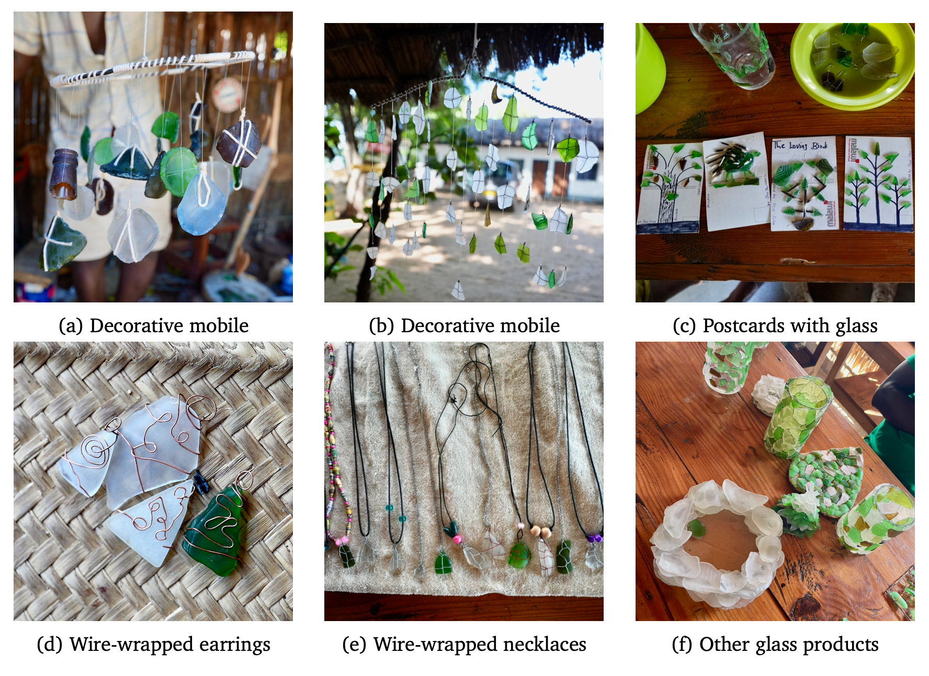
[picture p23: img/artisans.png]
Figure 2: Artisan trial outcomes


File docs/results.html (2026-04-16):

# Results

This page summarizes the performance, operational lessons and financial viability of the solar-powered glass tumbler based on data collected in February 2026.

## 1 Operational Performance

During its initial deployment from February 3 to February 27, the tumbler was operational for 118.5 hours. It successfully produced nine batches of tumbled glass, with each batch weighing approximately 20 kg. The process effectively transforms sharp, hazardous glass shards into smooth, safe “sea glass”.

## 2 Process Optimization

Experimental trials were conducted to determine the most efficient parameters for a high-quality finish:

- Optimal Duration: A 10-hour cycle is recommended to maximize quality. While much of the smoothing happens in the first few hours, “tumbledness” reaches a point of diminishing returns at the 8 to 10-hour mark (see Figure 1).
- Abrasive Media: The addition of a fine abrasive is mandatory for a nice finish. Trials using “just water” resulted in increased structural damage to the glass.
- Viability of Local Sand: Locally sourced fine sand performed nearly as well as industrial silicon grit. Given its zero cost and high availability in Malawi, local sand is the superior choice.



Figure 1: Glass progression

## 3 System Efficiency

- Power Draw: At the standard operating speed of 40 RPM, the system maintains a constant power draw of 79 W. Even at 100% speed, the draw was 107.1 W.
- Annual Yield: A single-panel (260 W) setup is projected to yield 4’274 kg per year, while a dual-panel (520 W) setup can reach 5’060 kg per year.

## 4 Financial Viability

The total material cost (CAPEX) for the standard 260 W system was $581.10. The Minimum Viable Price represents the break-even point required to cover all annual operating costs and amortized construction costs over a 5-year equipment lifetime.

Metric | 260 W Setup | 520 W Setup
Annual Yield | 4’274 kg | 5’060 kg
Minimum Viable Price (USD per 100 kg) | $4.94 | $4.40

## 5 Reuse and Creative Outcomes

Tumbled glass is already being integrated into the local economy in Cape Maclear. Local artisans have explored the material’s creative potential, producing jewelry and decorative items (see Figure 2).



Figure 2: Artisan trial outcomes

This project was supported by the Global Health Engineering Group at ETH Zurich (https://ghe.ethz.ch)

- (https://github.com/Global-Health-Engineering/glass-tumbler)
- (https://matrix.to/#/#ghe-open:staffchat.ethz.ch)

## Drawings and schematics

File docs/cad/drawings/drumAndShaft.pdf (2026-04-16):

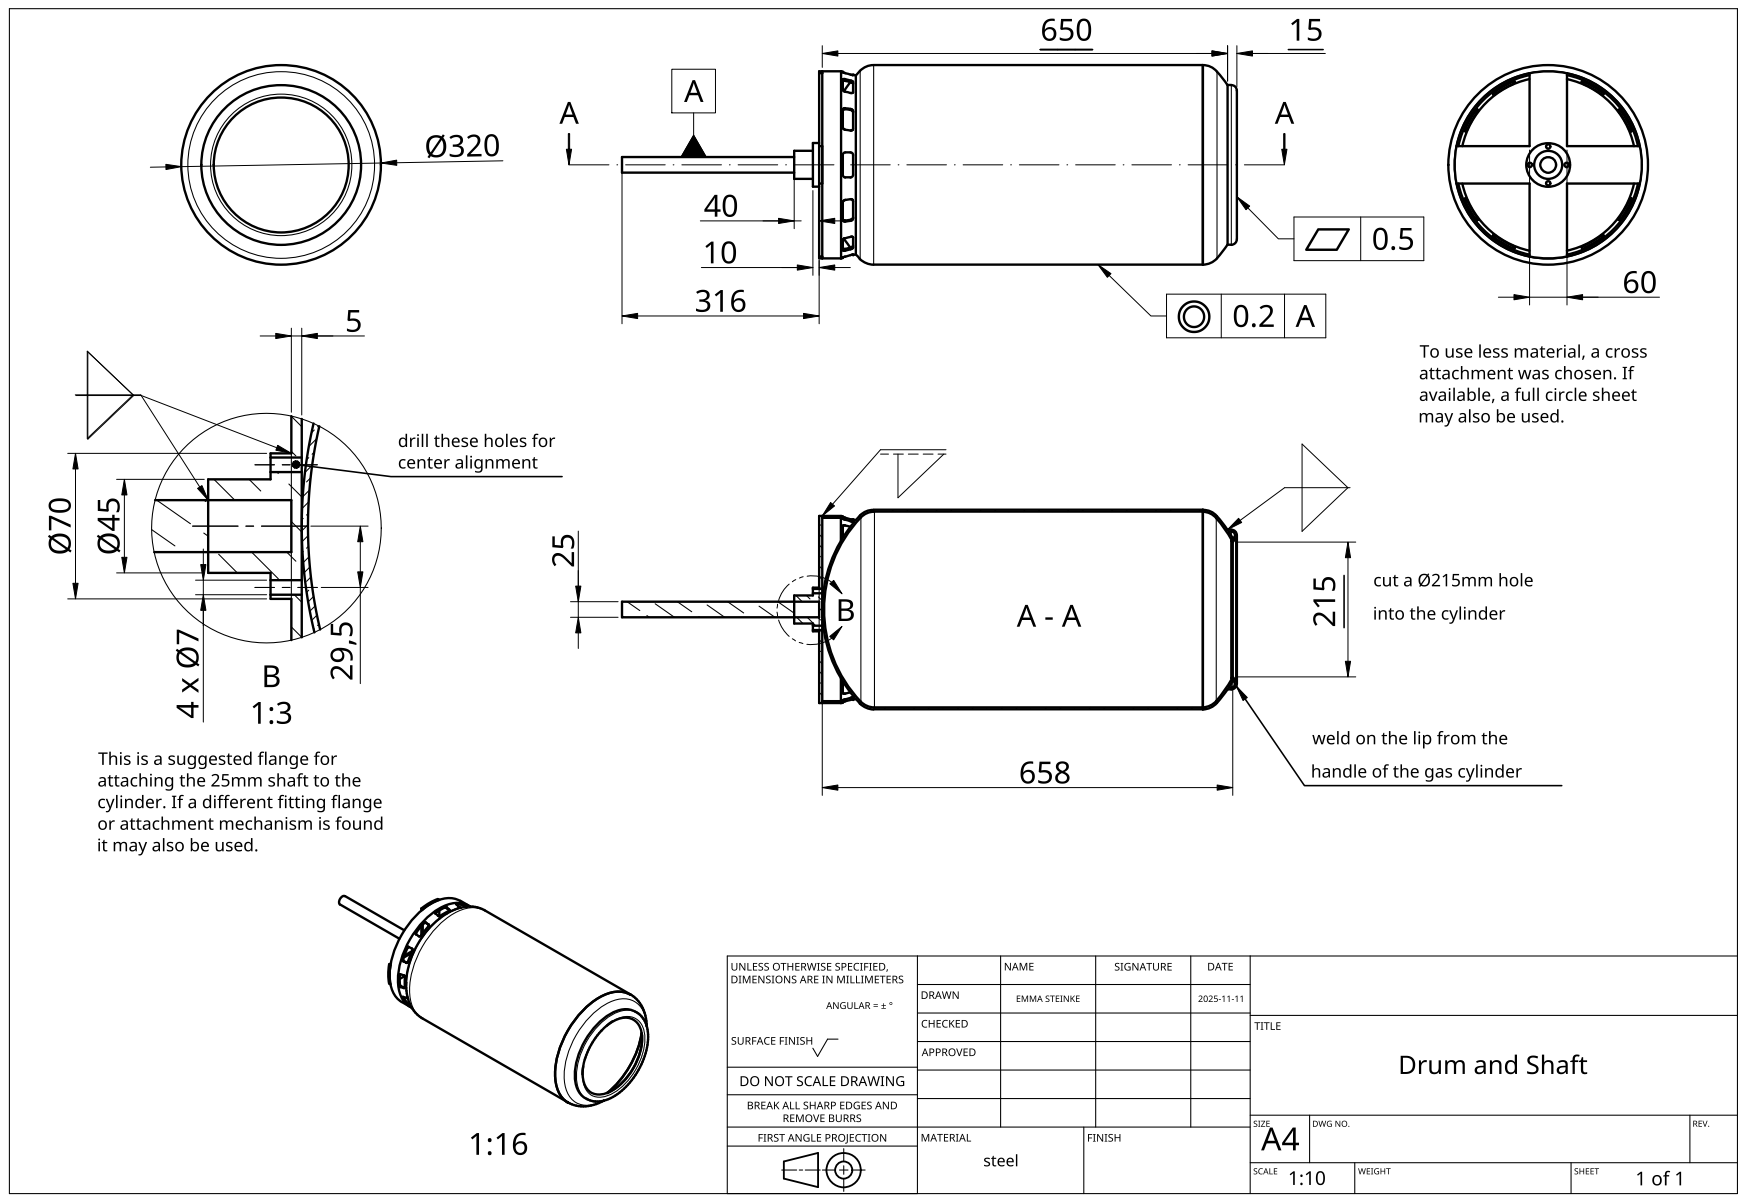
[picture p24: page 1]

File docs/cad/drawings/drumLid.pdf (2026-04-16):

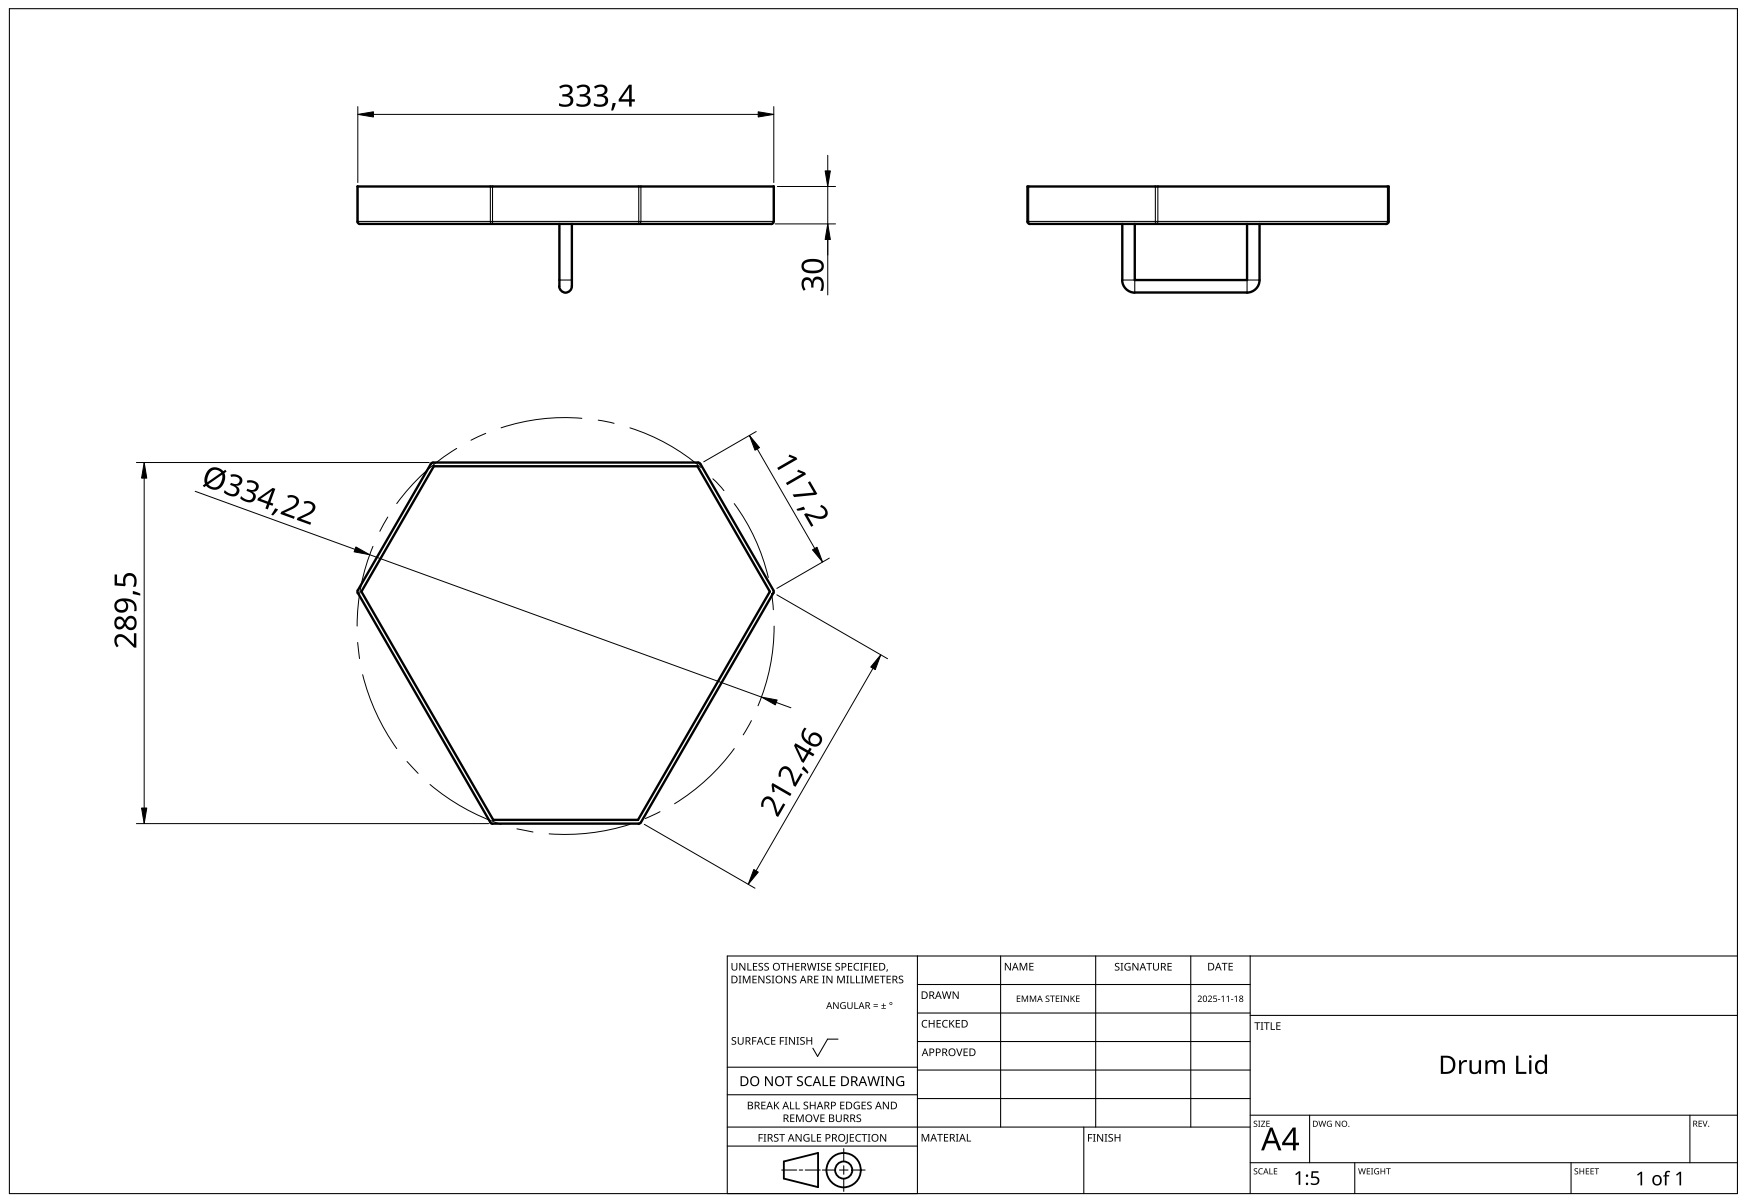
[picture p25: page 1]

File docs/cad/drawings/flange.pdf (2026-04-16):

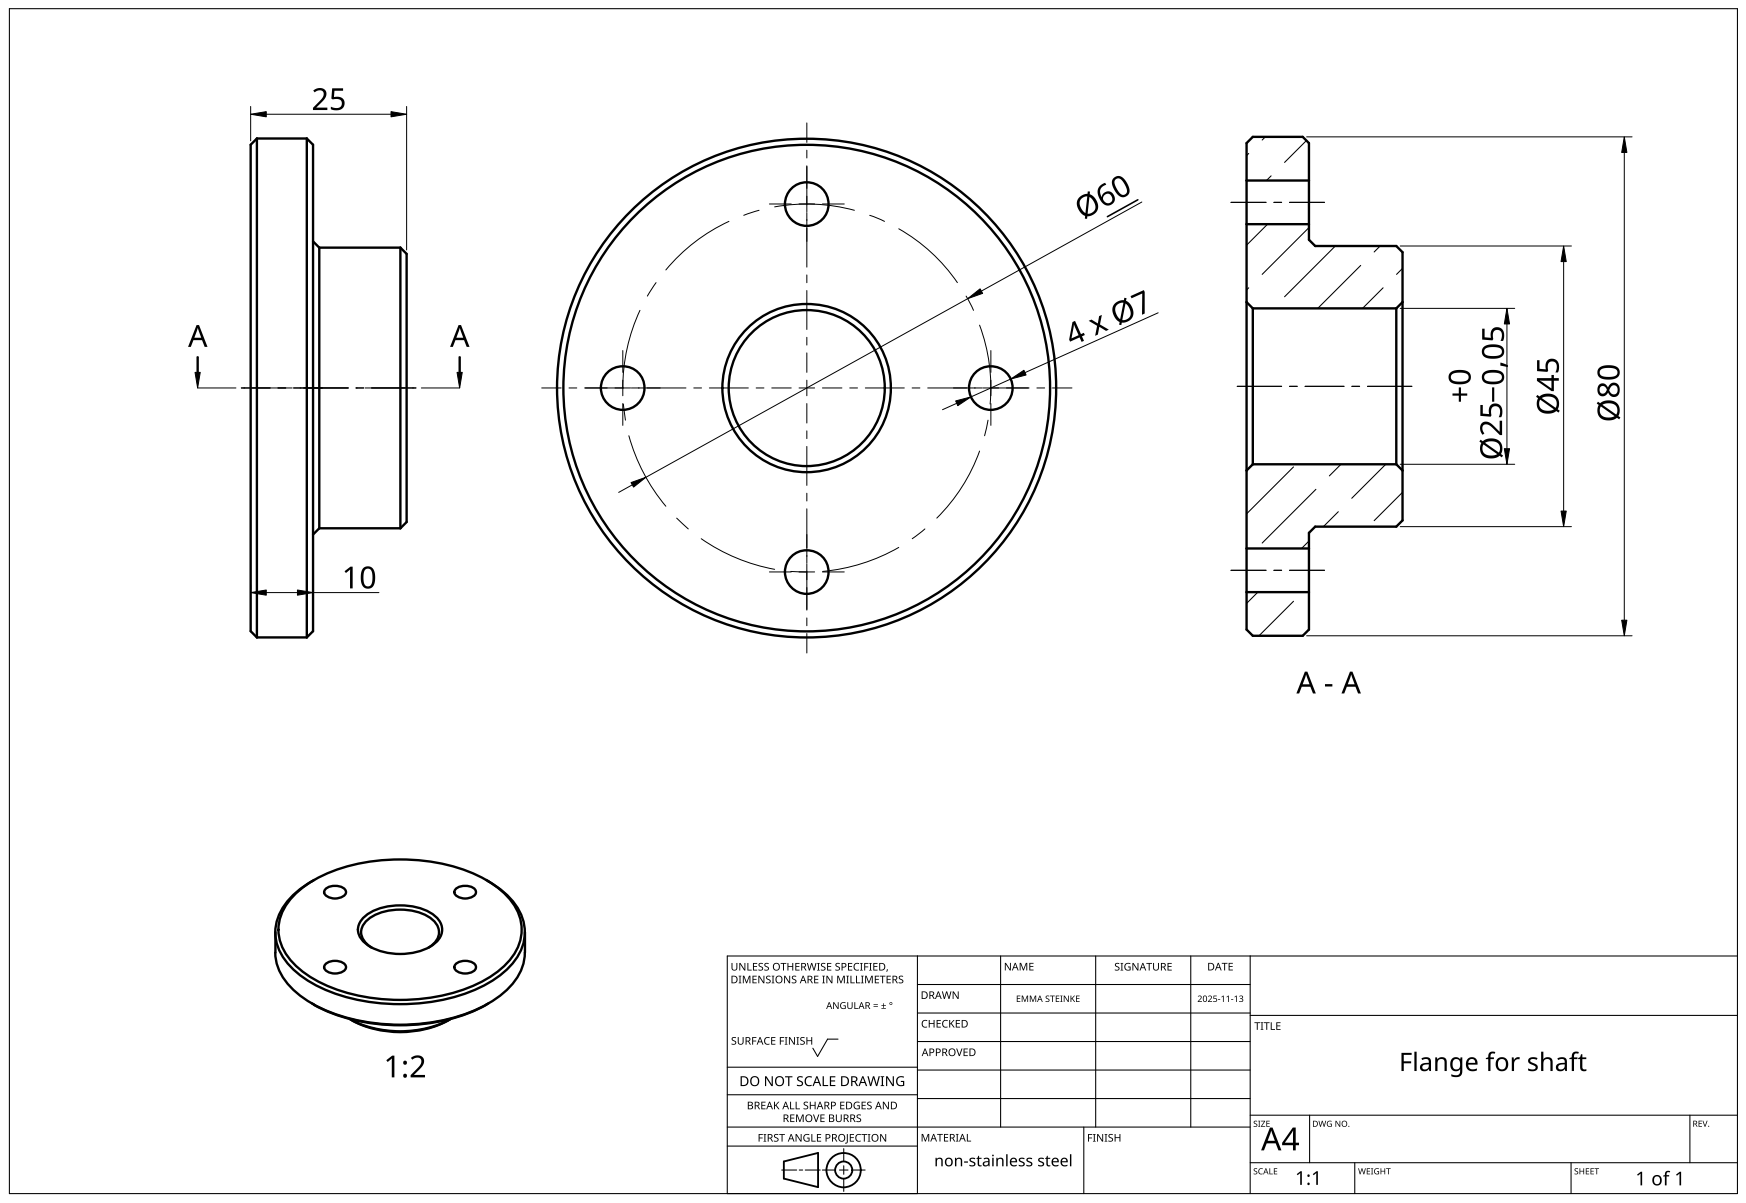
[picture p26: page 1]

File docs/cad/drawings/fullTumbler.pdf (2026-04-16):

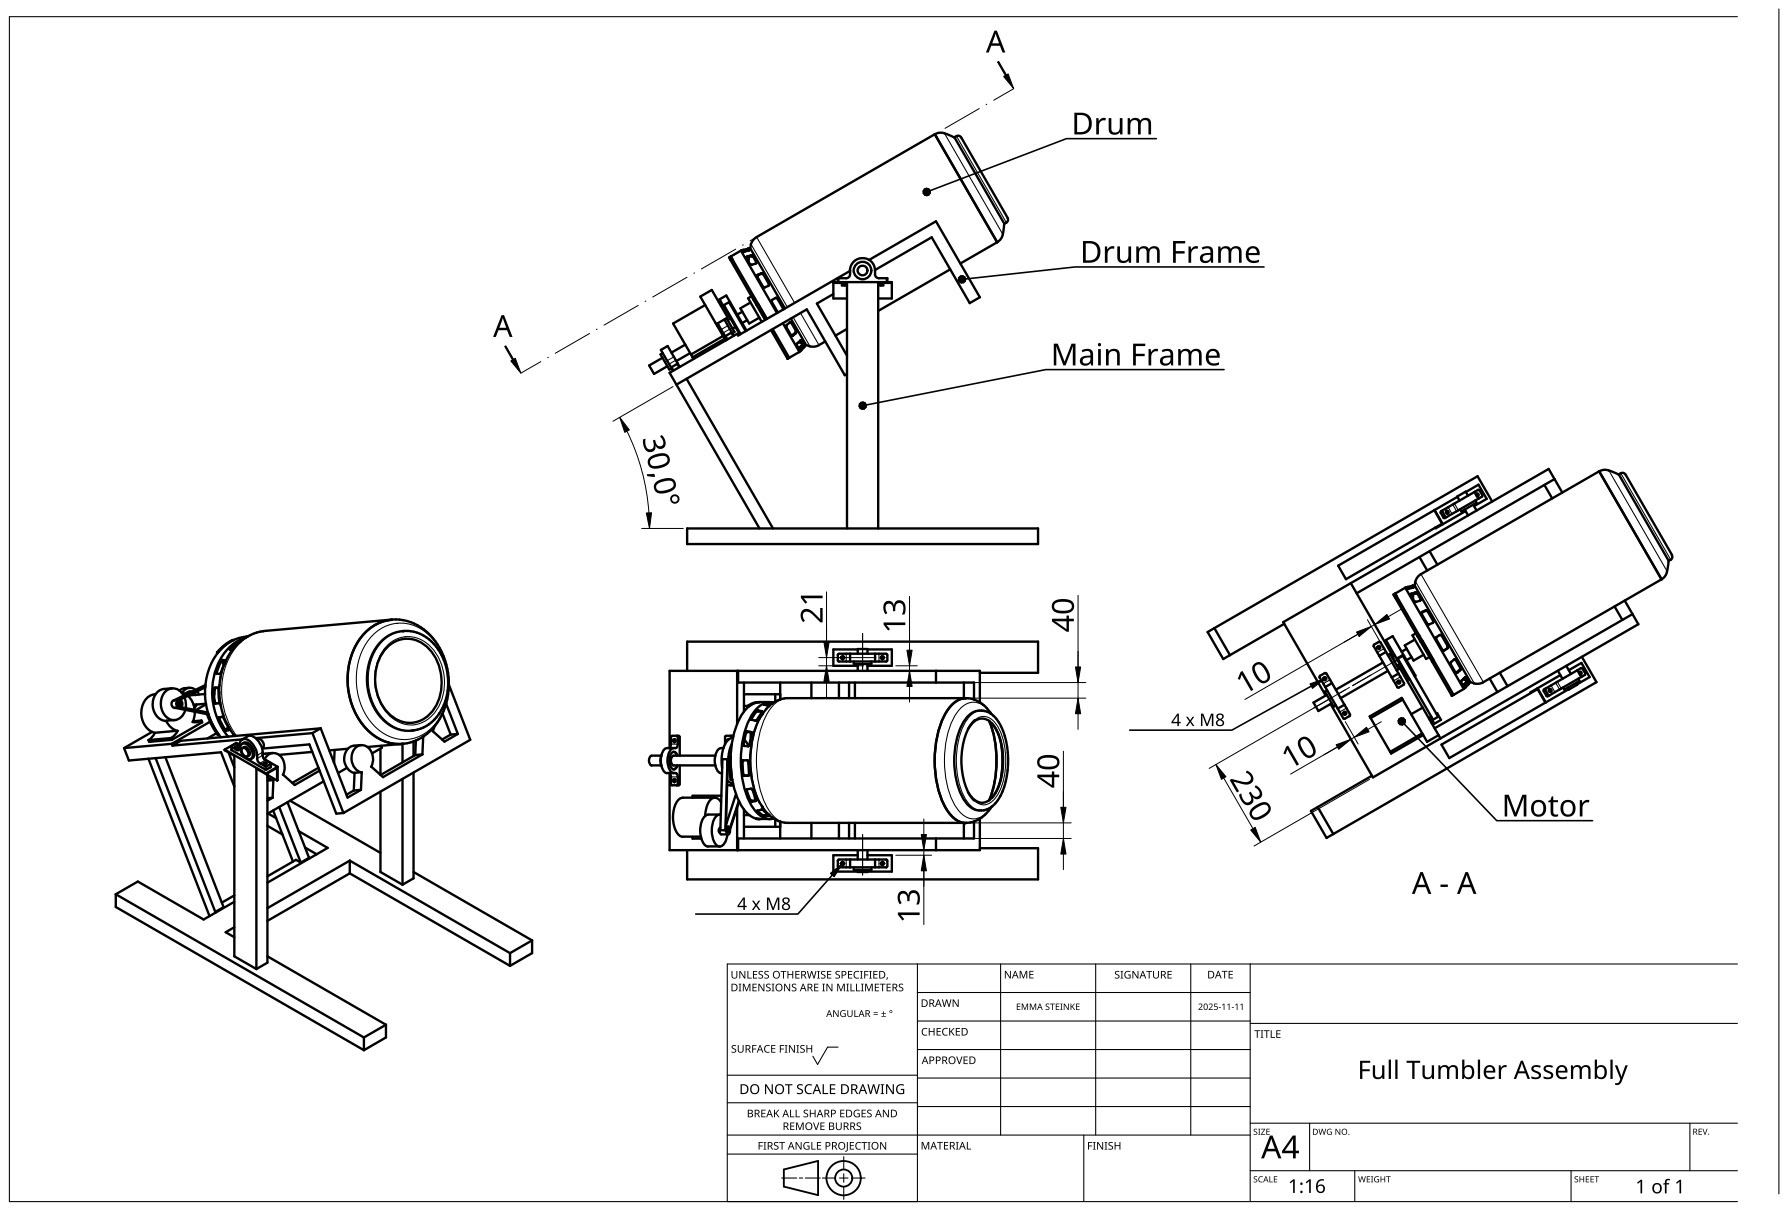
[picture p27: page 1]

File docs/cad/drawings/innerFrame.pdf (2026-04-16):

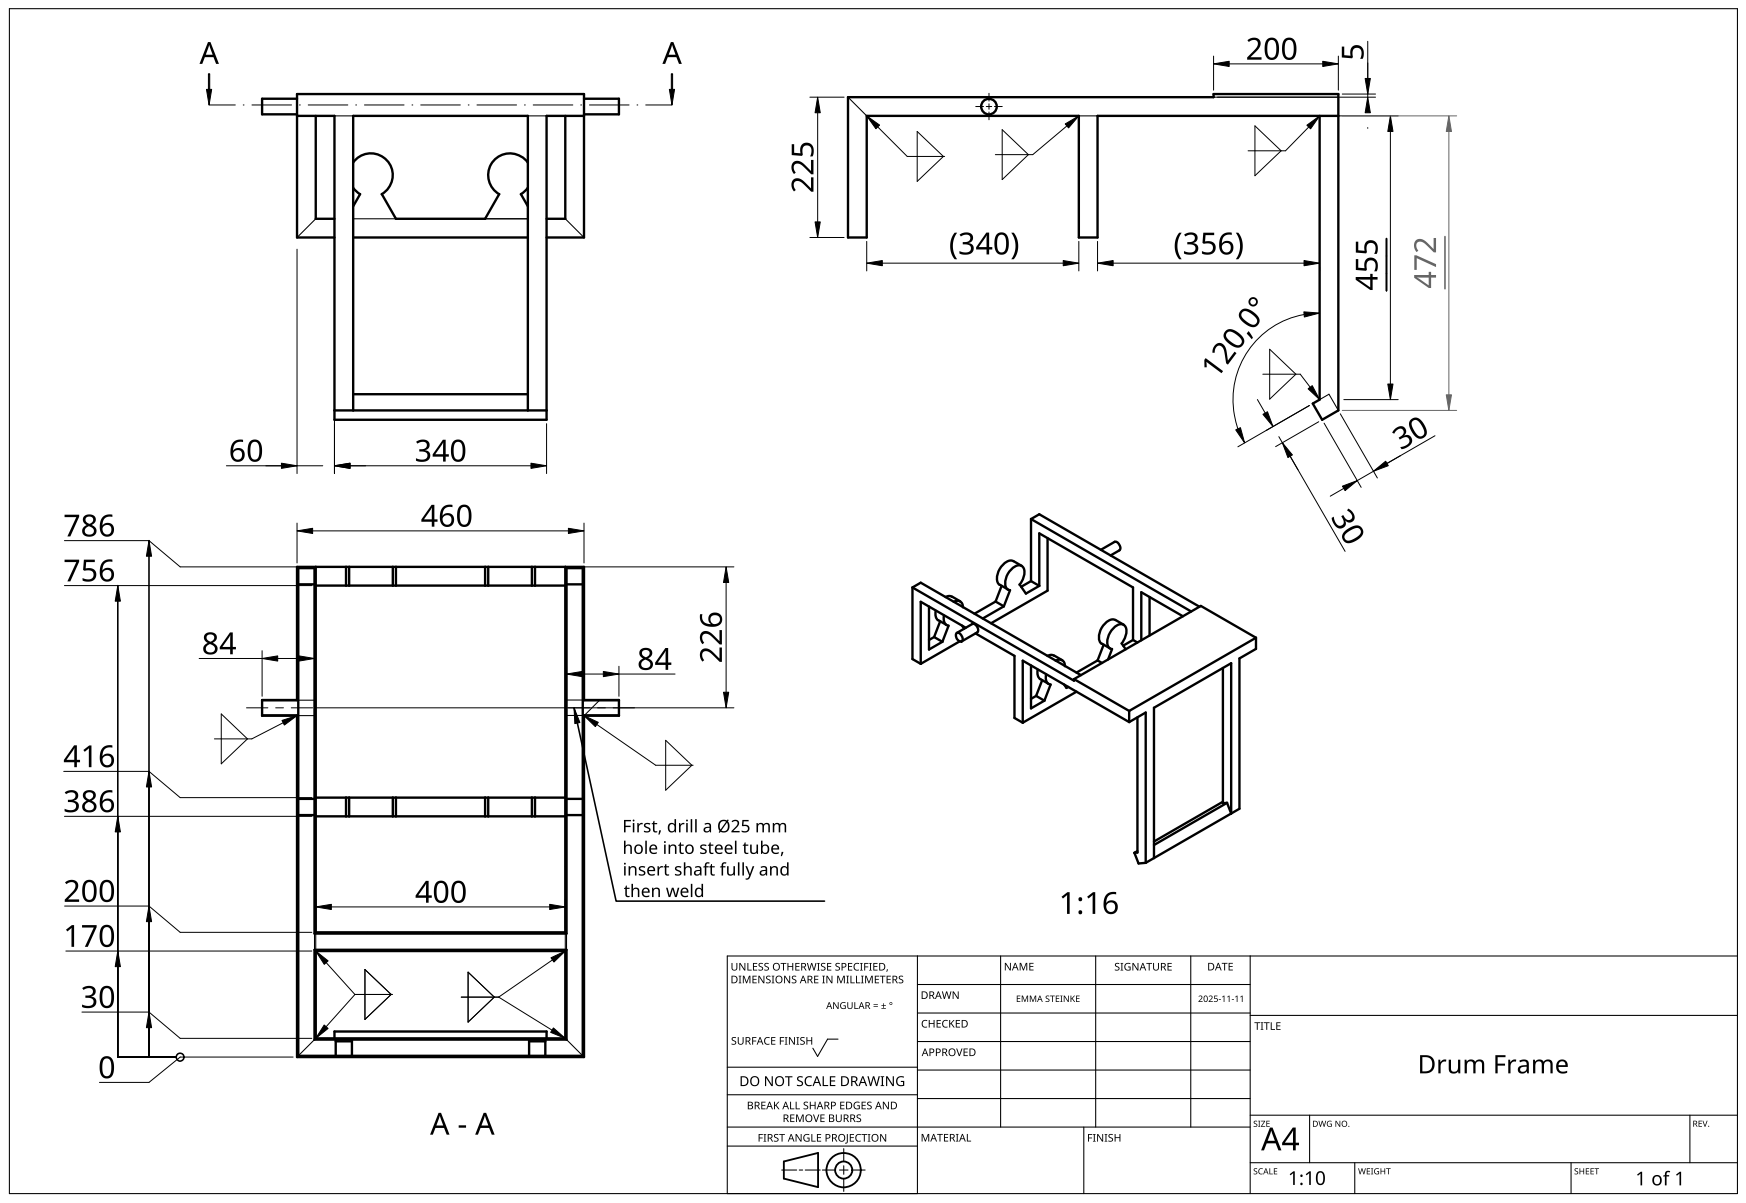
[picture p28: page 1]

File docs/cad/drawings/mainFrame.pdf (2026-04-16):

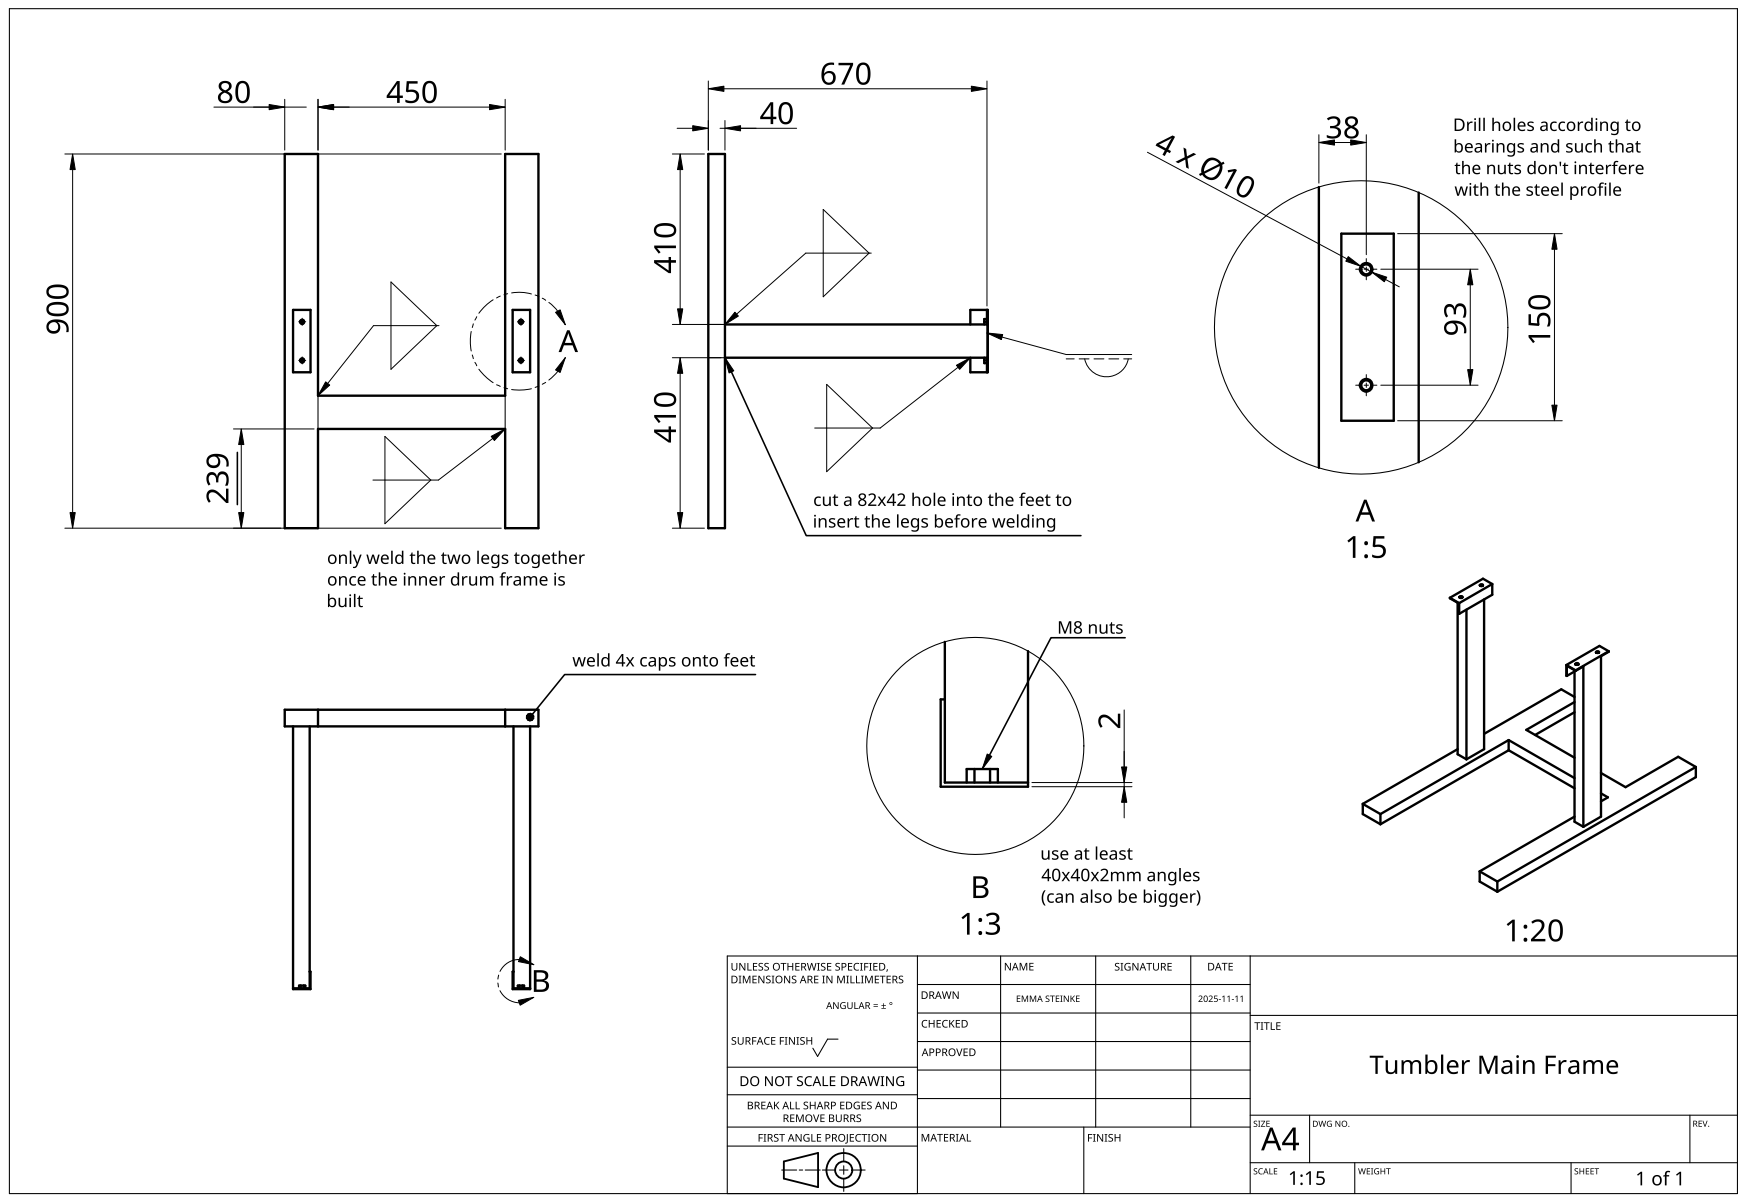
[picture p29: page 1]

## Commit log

2026-04-16 add project data and documentation
    [Drum Frame.step, Main Frame.step, Tumbler Assembly.step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]
2026-04-16 add rendered pages
    [Drum Frame.step, Main Frame.step, Tumbler Assembly.step]
